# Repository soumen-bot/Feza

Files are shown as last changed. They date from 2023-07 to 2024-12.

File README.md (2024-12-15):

# Feza

Constructed a UAV with S1223 airfoil that adhered to the requirements of SAE, India. The UAV was launched manually
from a circular location, which necessitated a focus on controllability during the design process. Priority was given to weight
optimization for the payload and ensured structural strength, while simultaneously striving for innovation

Final_draft.pdf has the final desing report for our UAV. 

Will be uploading video of flight and xflr analysis files soon

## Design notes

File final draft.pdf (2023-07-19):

DRONE DEVELOPMENT CHALLENGE 2023

DESIGN REPORT

DDC20230185 –
FEZA TEAM
MEMBERS

### 1. Marpati Varun Reddy 2. Mogli Pranav 3. Soumen Sinha 4. Vaishnavi Neela 5. Prem Ningombam 6. Vaibhav Naidu 7. Kshitij Gawande 8. Sravani Prabhala 9. Mallinath Ogirala

Survey No: 62/1A, Bahadurpally, Jeedimetla, Hyderabad, Telangana 500043

Dr Prasad Pokkunuri
Faculty Advisor

DATE (18 March 2023)

STATEMENT OF COMPLIANCE _

### SAEISS DRONE DEVELOPMENT CHALLENGE 2023

Certification of Qualification
Team Name | FEZA
Team ID | DDC20230185
College/University | Mahindra University
Faculty Advisor | Dr Prasad Pokkunuri
Faculty Advisor’s Email | prasad.pokkunuri@mahindrauniversity.edu.in

Statement of Compliance

As Faculty Advisor:

I certify that the registered team members are enrolled in collegiate courses.

I certify that this team has designed, constructed and/or modified the radio-controlled airplane with the intention to use this aircraft in the SAEISS Drone Development Challenge 2023 competition, without direct assistance from professional engineers, R/C model experts or pilots, or related professionals.
I certify that this year’s Design Report has original content written by members of this year’s team.
I certify that all reused contents have been properly referenced and is in compliance with the University’s plagiarism and reuse policies.
Signature of Faculty Advisor | Date (18 March 2023)
Signature of Team Captain | Date(18 March 2023)

Team Captain Information
Team Captain Name | Marpati Varun Reddy
Team Captain’s Email | Varunreddy00412@gmail.com
Team Captain’s Mobile: | 9110510760

Table of Contents

1. Appendix | 0
2. Introduction | 5
3. Objective | 5
4. Mission Parameters | 5
5. Research | 5
6. Airfoil Selection | 6
a. analysis | 6
b. wing airfoil | 6
7.wing planform | 7
8.wing configuration | 8
9.Wing loading and area selection | 8
10. Tail | 10

### 11. stability

a. final stability configuration | 12
12. electronics | 14
a. motor and esc selestion | 14
b. servo sizing | 18
c. battery selection | 18
d. red armin plug | 19
13. design | 20

a fuselage

19

20

b tail | 21
14 control surface sizing | 22
a ailerons | 22
b elevator | 23
c rudder | 24
15 manufacturing | 24
a material selection | 24
b packing box | 27
16 weight built up and balance | 29

APPENDIX

- v = Velocity of the aircraft.
- g = Acceleration due to gravity.
- Ws = Wing loading in kg/m2
- ρ = Density.
- b = Wing span.
- c = Mean aerodynamic chord length.
- S = Wing area.
- α = Angle of attack.
- Cm = Coefficient of moment.
- CL = Coefficient of lift.
- CMα = Coefficient of moment per degree of angle of attack.
- CLα = Coefficient of lift per degree of angle of attack.
- VH = Tail volume ratio (Horizontal).
- Vvt = Tail volume ratio (Vertical).
- Xn.p. = Distance for neutral point.
- Xc.g. = Distance for center of gravity.
- η = Efficiency of the tail.
- ε = Downwash angle.
- Iw = Wing setting angle.
- It = Tail setting angle.

### 1. INTRODUCTION

The report details the unmanned aerial vehicle (UAV) created by Team Feza for the 2023 Drone Design

Challenge organized by the Southern Section of the Society of Automotive Engineers India (SAEISS). The

competition's objective is to provide engineering students with practical challenges that they may encounter

during their academic tenure by tasking them with researching, developing, designing, constructing, and

producing a prototype of a fixed-wing UAV that meets the practical and mission requirements specified by

SAEISS. The process also enables students to acquire vital technical and interpersonal skills.

### 2. OBJECTIVE

Team Feza's objective was to construct a UAV that adhered to the requirements outlined in the rulebook.

The UAV would be launched manually from a circular location, which necessitated a focus on

controllability during the design process. The team also prioritized weight optimization for the payload

and ensured structural strength, while simultaneously striving for innovation.

### 3. MISSION REQUIREMENTS

SAEISS aimed to motivate undergraduate students to create a UAV capable of lifting the maximum

payload according to the specified regulations. The UAV's weight limit, not including the payload, was

set at 1.5 Kgs, and it had to fit inside a box with sides less than 3ft. The UAV had to be launched

manually from a designated launch circle and complete a full 360 circuit using only a 3s battery for

power.

### 4. RESEARCH

Our team has been participating in the micro class for three generations now and in the past, we prioritized

the assembly of parts and structure. For our last project, we opted for a high wing rectangular configuration

and utilized a complete monocoque fuselage. However, this time around, we aimed to simplify the design by

utilizing a side paneled fuselage and adhering to the SAEISS rule book and Micro class constraints. Our

inspiration came from the manufacturing processes of last year's Regular and Micro planes. Previously, we faced challenges in achieving a balanced center of gravity and installing the battery. To simplify the

assembly process, we have designated specific positions for electronics and created separate holding spaces

for them.

### 5. AIRFOIl SELECTION

a. analysis

To narrow down the list of previously chosen airfoils, a number of flight determining factors are taken into

account. These factors include the Coefficient of lift at ‘0’ angle of attack, Stall angle, Maximum coefficient

of lift, Manufacturing limitations, and the Average drag coefficient across a range of Reynolds numbers. The

analysis is conducted using Reynolds numbers ranging from 10,000 to 500,000 and an angle of attack

between -10 to 30 degrees.

b. Wing airfoil

To pack as much lifting capabilities in to the plane, Airfoils with high cl values at low Reynolds-number are

researched. For preliminary analysis of wing and horizontal stabilizer options, several cambered airfoils were

considered. These included EPPLER's E423, E421, and E420, SELIG's S1223, S1223rtl, and S2027,

WORTMANN's FX74-CL5-140 and FX63_137, AG35, CH10, NLF 0115, NACA 6409, Kenmar-il, Kc135

winglet, and LNV 109 A. After evaluation, EPPLER's E423, E421, and E420, SELIG's S1223 and S1223rtl,

and CH10 were found to have the highest capabilities for cl and cl/cd at low Reynolds numbers. Of these,

S1223 had the highest cl, as well as a high Cm. Despite the high Cm, the team chose to go with a high Cl

airfoil in order to build the plane as compactly as possible.

S1223 –

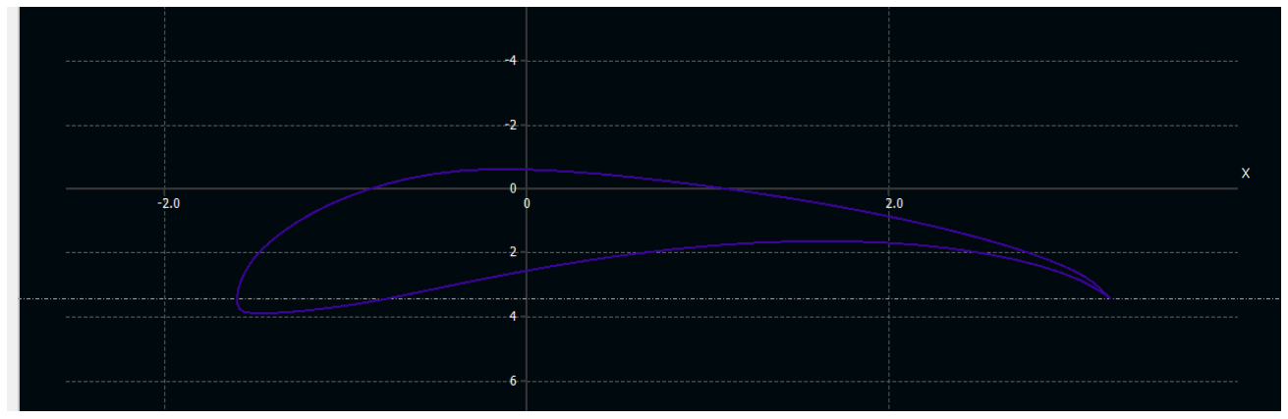
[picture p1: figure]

Thickness | Max. Thick.pos. | Max. Camber | Max. Camber pos.
12.14% | 19.82% | 8.67% | 49.05%

Table:1 tabular data of the shape of the Airfoil S1223

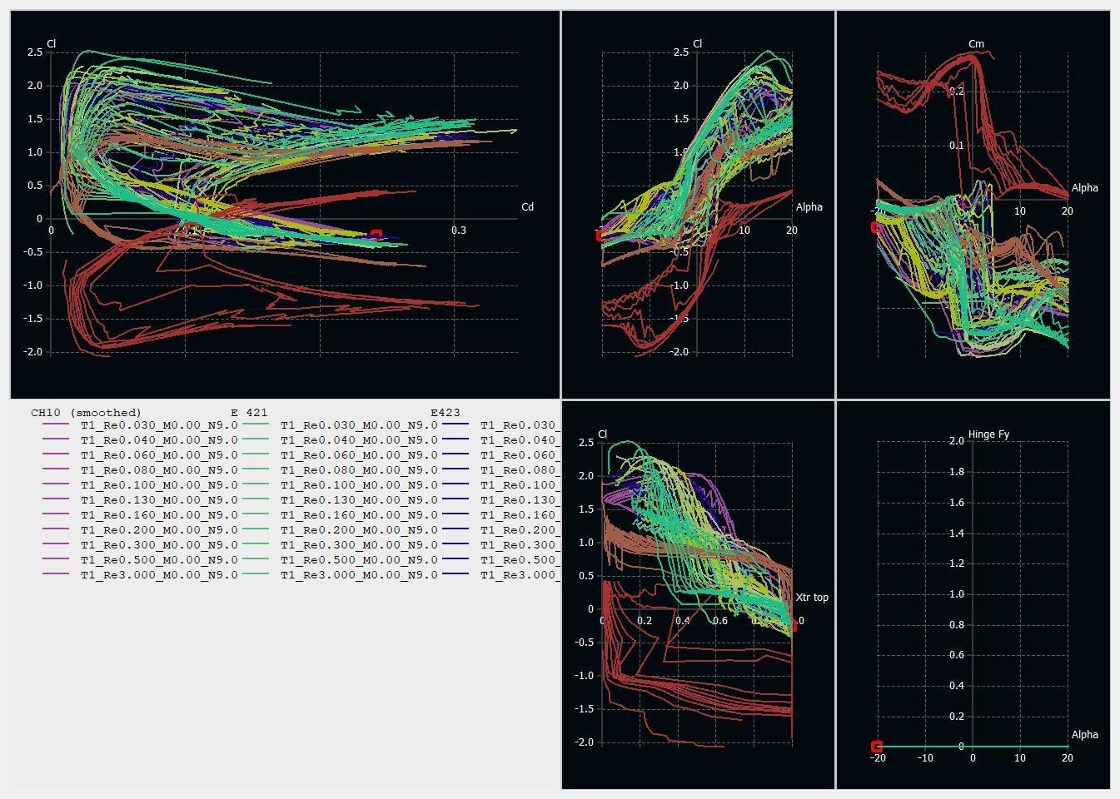
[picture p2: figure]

The graphs above primarily show the relationships between cl and cd, cl and alpha, and cm and alpha for types of foils: S1223 and NACA0012. EPPLER's E423, E421, E4203 and S1223rtl, and CH10

### 6. WING PLANFORM

After conducting a detailed analysis and comparing different planforms, a rectangular wing configuration was

selected. The comparison revealed that the drag reduction offered by a tapered wing over a rectangular wing was

minimal. Additionally, while elliptical wings have the advantage of stalling uniformly across the entire wing

instead of at the tips first, manufacturing them is more complex than a rectangular wing. A delta wing was not

chosen due to the stringent design, size, and manufacturing requirements it demands.

### 7. WING CONFIGURATION

The High wing configuration has been selected among the three options of Low, Mid, and High wing.

This is because of its inherent keel effect or pendulum effect, resulting from the center of gravity being

lower than that of the center of lift. Additionally, the Low wing configuration is avoided to prevent the

UAV from landing on its wings. Furthermore, manufacturing the Low and Mid wing configurations to

be longitudinally stable can be challenging. Based on our past experience with a Mid wing

configuration, the UAV began to wobble and flutter its wings, whereas the High wing configuration

offers a slight advantage for easy reinforcement. Another design advantage of the High wing

configuration is that the wing can be slid on top of the plane and secured to complete the aircraft.

### 8. WING LOADING AND AREA SELECTION

Wing loading is the ratio of Aircrafts weight to its area. It helps determining the stall speed of the aircraft

the above equation gives us the wing loading

Assume Cl =0.762 . ρ = 1.29 , ( values of Cl and ρ are chosen so that they cover most of

the range of the flight.)

Table 5.1: Velocity vs Wing loading of the aircraft
Velocity (m/s) 5 | 7.5 | 10 | 12.5 | 15 | 17.5 20 | 22.5

Wing

loading (kg/m²

)1.25 | 2.82 5.01 7.83 | 11.28 | 15.35 20.06 25.38

A step size of 0.25Kg is considered to calculate the wing area at different

velocities that can be acquired from hand launch, with plane weight up to 3 Kgs

Table 5.2: Area of the wing in m² based on weight and velocity of the aircraft.

Velocity (m/s) | 5 | 7.5 | 10 | 12.5 | 15 | 17.5 | 20 | 22.5
Mass = 1.5 kgs 1.2 | 0.53 | 0.29 | 0.19 | 0.132 0.09 | 0.074 0.059
Mass =2 kgs | 1.6 | 0.70 | 0.39 | 0.255 | 0.177 0.13 | 0.099 0.078
Mass = 2.5 kgs 2 | 0.88 | 0.49 | 0.319 | 0.221 0.16 | 0.124 0.098
Mass = 3 kgs | 2.4 | 1.06 | 0.59 | 0.383 | 0.265 0.195 0.149 0.118

We fixed our wingspan to be 120 cm to accommodate the wing loading capacity and still

be able to fit in the box with all sides less than 3ft, through extensive analysis by XFLR5

we arrived at a wing span of 0.25m²
that is a chord length of 25 cm.

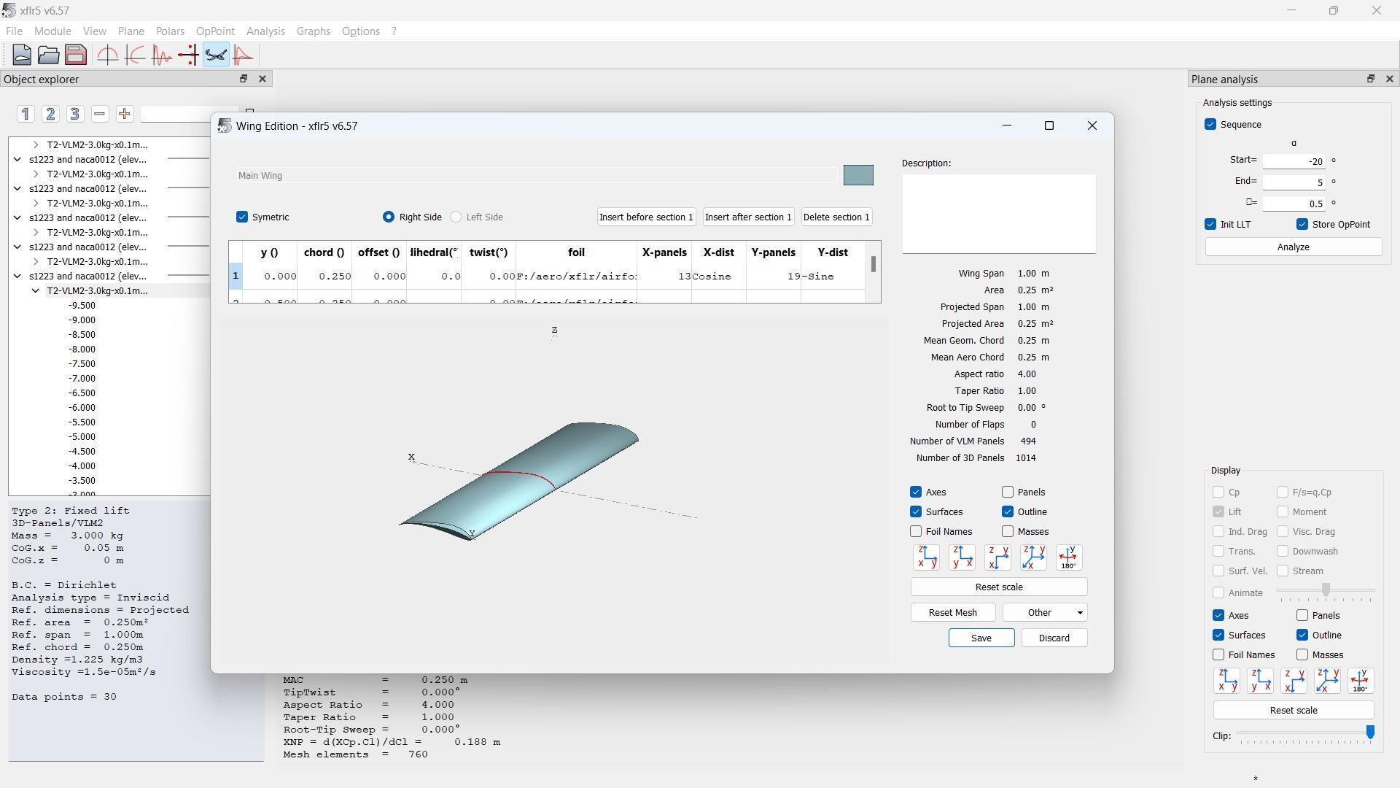
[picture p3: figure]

### 10. Tail

We chose to use the standard Tail configuration for our plane, which consists of two components -

the horizontal stabilizer and the vertical stabilizer. These parts play a critical role in guiding and

maneuvering the plane during flight. The Tail is an essential part of the plane that helps to maintain

its orientation and keep it on the desired flight path in a passive manner. This is achieved by

generating a moment around the Cg (center of gravity) through the deflection in orientation caused

by any disturbances.

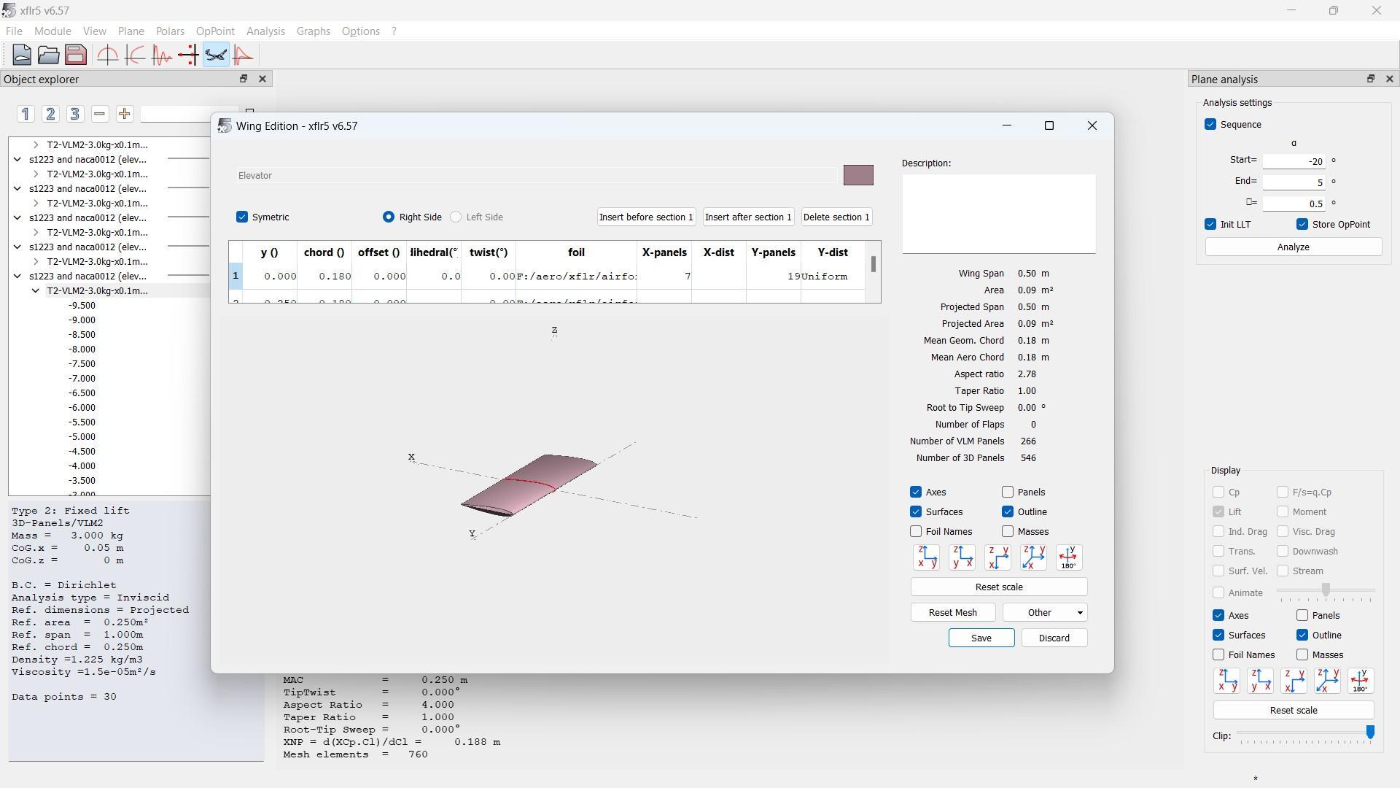
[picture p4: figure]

We decided to use the NACA0012 airfoil for the elevator of

our plane due to its effective production of pitching moment and minimal drag. Our objective was

to minimize the size of the horizontal stabilizer while still balancing the wing moment, and as a

result, we were able to achieve satisfactory longitudinal stability.

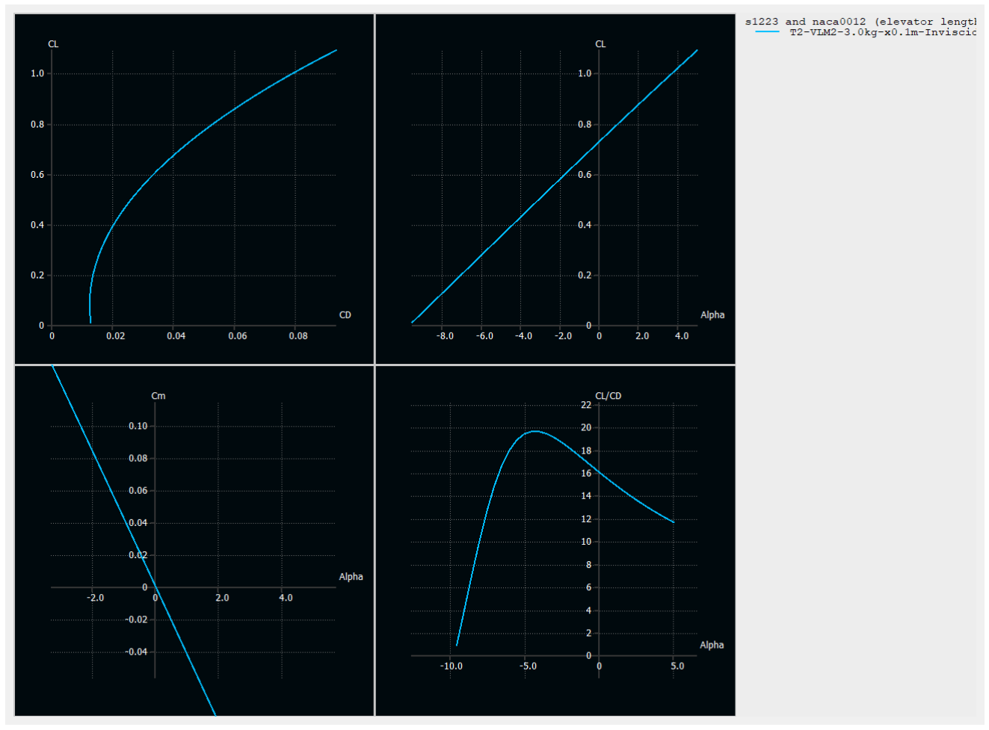
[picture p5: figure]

the above picture gives you the flight characteristics of our plane

FINAL STABILITY CONFIGURATION

After the detailed and calculate evaluations of all the possible configurations of tail and the area of

wing being 0.25 m2,the following configuration of the plane was achieved:

Table: Aircraft properties for stability configuration.

Name | Class | Numerical Value

Wing Properties

Chord Length

Wing area

Wing span

Wing setting angle

0.25m

0.25 m2

1.2m

0

Horizontal tail properties | Chord Length Tail span Tail setting angle | 0.180m 0.5m 0
Vertical tail Properties | Chord Length Tail Span | 0.180m 0.25m

### 1. Electronics

a. Motor and ESC selection:

After considering the mission objectives and regulations, we opted for a DC brushless outrunner motor

with a low kV rating. We selected a low Kv motor because it is more suitable for airplanes that fly at

slower speeds, as it provides higher output torque. This enables us to use a larger propeller with a small

pitch, which is typically used in short takeoff and landing aircraft. In our decision-making process, we

also took into account the weight of the aircraft, including any cargo, the necessary thrust (keeping battery

limitations in mind), and the required power output.

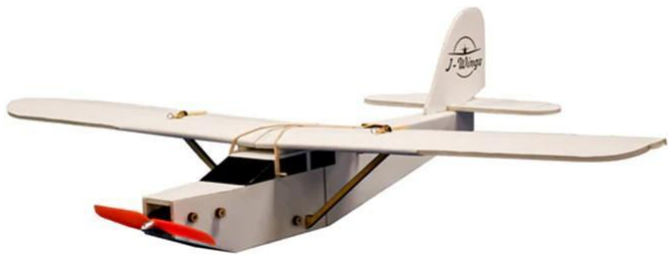
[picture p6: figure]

Type of airplane | Thrust-to-weight ratio
Glider/Trainer | 0.35 to 0.55
Scale Flight | 0.60 to 0.70
Sport and Slow acrobatic | 0.70 to 0.80
Acrobatic | 0.80 to 1.00
Jets and 3D | 1.00 to 2.5

Our study found that the correlation between power (measured in watts, W) and thrust (measured in grams,

g) is directly linked to the Kv rating of the motor. Nonetheless, the scatter of data points in the graph may

differ depending on the propeller pitch. Fundamentally, when the Kv rating increases, a greater amount of

power is needed to produce the same thrust. This is because using a higher Kv motor necessitates a

reduction in propeller diameter.

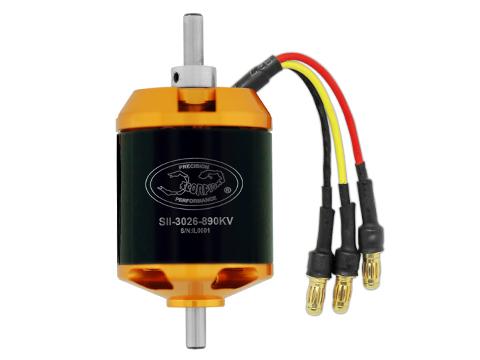
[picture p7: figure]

Once you know the weight of your aircraft, the process consists of several steps:

- Determine the desired thrust-to-weight ratio.
- Calculate the amount of thrust required for your plane.
- Decide on the desired speed of your aircraft (fast or slow).
- Choose a Kv value that aligns with your objectives.
- Use the Kv value to identify the Power/thrust ratio.
- Determine the power (in watts) required to generate the necessary thrust.
- Based on the selected values for Kv, thrust, and power, select a motor from a

reputable manufacturer.

·Either follow the recommended propeller specifications for the chosen motor or use an

appropriate method to select a suitable propeller.

Calculating thrust:

Thrust= Weight*thrust/weight ratio | (The thrust/weight ratio of an acrobatic plane

is 1)

Thrust= 1900*1 = 1900g of thrust

As mentioned in the beginning of this section, we prefer a low kv value motor because it better suits

the plane that fly at slower speeds. So, we chose a motor the 1000kv specification.

To go further in selecting a motor, we need the power of our motor.

Calculating power:

Power = thrust* power/thrust ratio

Power/thrust ratio=

0.17*(kv/1000)+0.09

=0.17*(1000/1000)+0.09

=0.26w/g

Now, going back to calculating power:

Thrust is found to be 1900g. => 1900*0.26= 494 watts

So, in conclusion, referring to the calculations made, we are looking for a motor with the following

specifications:

1. 1000kv
2. 1900g of thrust
3. Wattage of 494w.

The motor we finalized isScorpion SII-3026-890KV (V2)

[SII-3026-890KV]

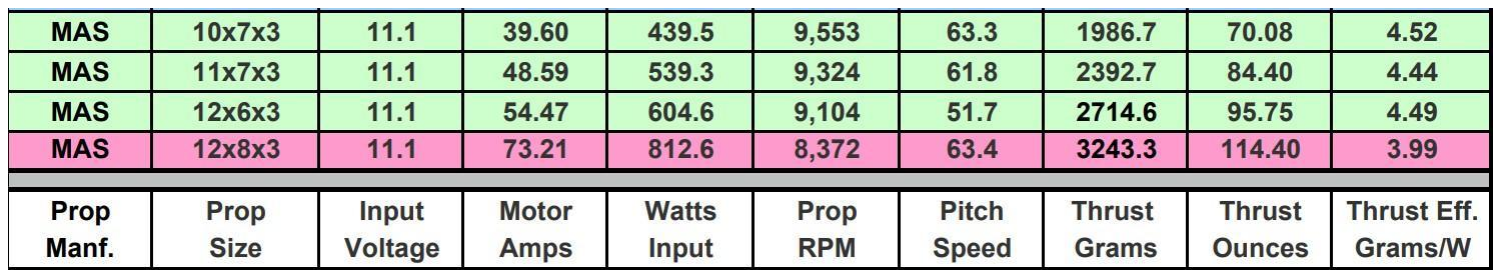
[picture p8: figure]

The essential factor to consider while choosing an ESC was that the motor would not

draw more current than the ESC's maximum rating. The motor consumes 70A of current

at maximum power. We picked a Readytosky 80A ESC 2-6S Brushless ESC Speed

Controller

which can support 80A rating based on this

b. Servo sizing:

The selection of servos for our aircraft is dependent on various factors such as the weight of the

flight, the dimensions of the wing, and the required thrust. Additionally, we take into consideration

the sizing of control surfaces and the type of battery used. The decision to choose a specific servo is

also influenced by its rated speed, supply voltage, and the amount of output torque required.

C

2V

2L sin(s1) tan(s1)
T = 8.5 × 10
−6 ( | tan(s2)

)

c. Battery selection
The battery was selected based on the restrictions according to the rulebook supplied and the

requirements of the motor and servos selected such that it be sufficient for a 5-minute flight

keeping a 20% error margin. With maximum current required as 36A, 3S (due to rule book

restrictions) 11.1V and the motor selected we researched batteries and decided to use the Orange

2200mAh 3S 30C/60C Lithium polymer battery Pack (LiPo) as it best fit our requirements and

the manufacturer was well known for its quality.

d. Red arming plug
An arming plug, essential for safety, is a small plug, fit in the flight hardware to enable functions

that, for instrument or personnel safety. Arming switches are used for isolating the battery from

outside of the aircraft. The arming plugs are fabricated by the team to facilitate enough wiring

length and to accommodate xt60 male plug from battery and bullet connectors from ESC and The

necessary holes have been made for installation during flight so that it can be easily activated

before flight.

### 13. Design

During our previous participation in the competition, we utilized a monocoque structure to

construct a lightweight aircraft. However, we faced challenges in installing the necessary

electronics such as the battery and ESCs. To overcome these difficulties, we opted to build a

sidepaneled fuselage that resembles a rectangular

box-like structure for this year's competition. Our previous fuselage design consisted of two major

elements, which were the ribs and longerons, and we avoided using stingers to reduce the

complexity of the chassis. For this year's competition, we simplified the manufacturing process by

eliminating all the ribs and spars, and instead, we constructed a high wing configuration plane.

a. Fuselage

Our goal for the fuselage was to achieve both durability and lightness. After careful deliberation, we

determined that implementing a truss system would be the most effective solution. This approach

would enable us to reduce the amount of material required while still maintaining the necessary

structural integrity. Our team conducted extensive research to acquire a comprehensive

understanding of truss systems and to develop a suitable design for the fuselage. One of the

innovative ideas we implemented this year was applying the truss theory to reinforce the

structural strength of the fuselage.

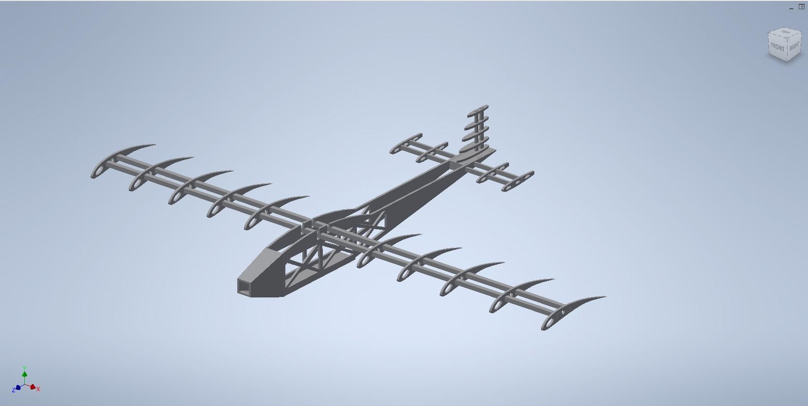
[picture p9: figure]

b.Tail

This year, we created a high-quality CAD design for the tail of our aircraft, which utilizes an innovative

approach where the fuselage walls are connected by a V-shaped ramp structure that can support both the

horizontal and vertical stabilizers through intrusions. With this design, we expect to have decreased the

amount of stress and shear on the tail compared to previous designs, and also made it easier to attach the

rudder and elevator with less effort and time required during the plane manufacturing process.

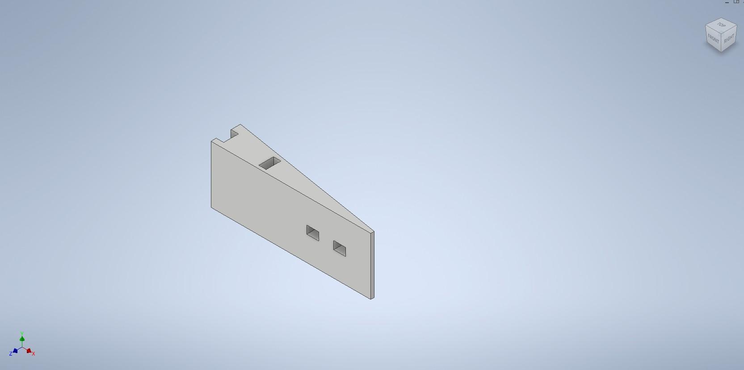
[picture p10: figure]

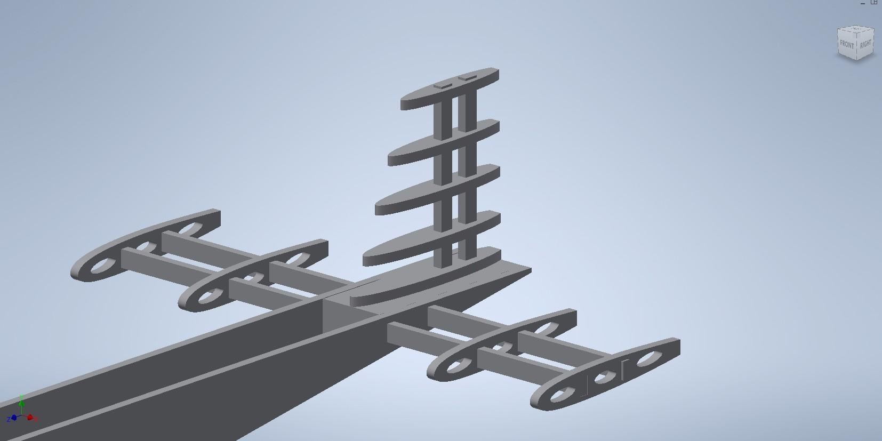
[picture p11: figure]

### 14. CONTROL SURFACE SIZING

AILERONS:

The 4 main parameters to be considered while designing the ailerons are the aileron planform

area (Sa), the aileron chord/aileron span ( Ca/ba), the maximum up and down deflection ( +(or)-

Dmax ), and the location of inner edge of aileron along the wing span (bai).

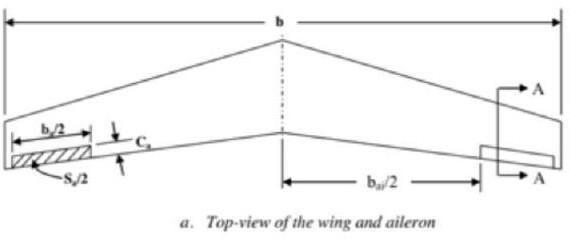
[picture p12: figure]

To set the proper dimensions of the ailerons a general guideline was followed. The typical

values for these parameters are as follows:

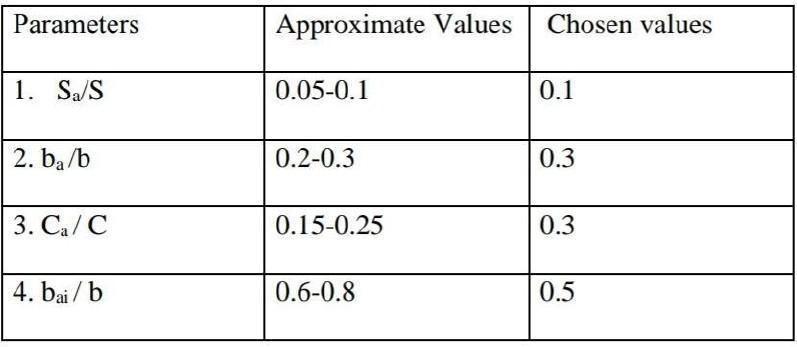
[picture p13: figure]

The value of Sa/S (area of ailerons by area of wing) was taken as 0.1. This was to maximise area of the aileron to minimise time to achieve a certain bank angle, resulting in a higher manoeuvrability.
The
issue with having a larger aileron is the load the actuators have to take will be higher. Thus, servo sizing was crucial.
The ratio of ba/b (aileron length to wing span) was taken as 0.3 based on other aircraft data. The ratio of Ca /C (aileron chord length by wing chord length) was taken as 0.3. The area of the aileron was to
be around 0.1 of the wing area. Thus, ba and Ca were varied to ensure an optimal case for a
desired area. The ratio of bai/b was taken as 0.5 to ensure the aileron doesn’t end at the wing tip.
This was to decrease excess wing tip vortex, which is caused due to the aileron ending at the wingtip. The aerodynamically accepted range of maximum deflection of the ailerons is 300. Increasing the angle beyond this would cause flow to separate, causing the surface to stall.
Thus, after running multiple iterations, it was decided the aileron would have the following values Ca = 75 mm ba = 600 mm bai = 180 mm
Thus, ailerons dimensions were 180 mm x 75 mm. Positioned at distance of 120 mm from either wing tip.
a. Elevator:
The rule of thumb is that the elevator should be 10%-25% of the area of the horizontal stabilizer. We chose the lower bound to keep the area of the elevator as less as possible so as to ensure less sensitivity to flying environments. Essentially, the span of the elevator=span of horizontal stabilizer. Only the chord of the elevator will be different. Length of chord=20% of length of chord of horizontal stabilizer. As the horizontal stabilizer was designed to have a span of 300 mm and a chord of 75 mm, the elevator was sized at the

following□ span = 0.5m

chord = 0.180m

a. Rudder:
The rule of thumb is that the rudder should be 10%-25% of the area of the vertical stabilizer. We chose the lower bound to keep the area of the rudder as less as possible so as to ensure less sensitivity to flying environments. So, the span of the rudder=span of vertical stabilizer. Only the chord of the rudder will be different. Length of chord=20% of length of chord of vertical stabilizer. As the vertical stabilizer was designed to have a span of 150 mm and a chord of 75 mm, the rudder
was sized at the following
Span = 0.25m
Chord= 0.180m

### 16. Manufacturing

a. Material selection

As stated in the beginning of the report, the weight of the plane designed for ADC 2022 was barely within the stipulated limits. So, the team did an analysis of areas to reduce weight. Hence, research was done from scratch on the design which resulted in the selection of Balsa wood. Balsa wood is an orthotropic material often used for hobby level UAVs due to its light-weight and decent strength. The mechanical properties of Balsa are as follows:

Table 6: Mechanical Properties of Balsa Wood

Density | 0.16 g/cm³
Ultimate Tensile Strength | 1.00 MPa (perpendicular to grains) 73.00 MPa (Axial)
Compressive Strength | 1.00 MPa (Perpendicular to grain) 6.90-9.00 MPa (axial)

Flexural Modulus | 2.55-3.17 GPa (Static Bending)

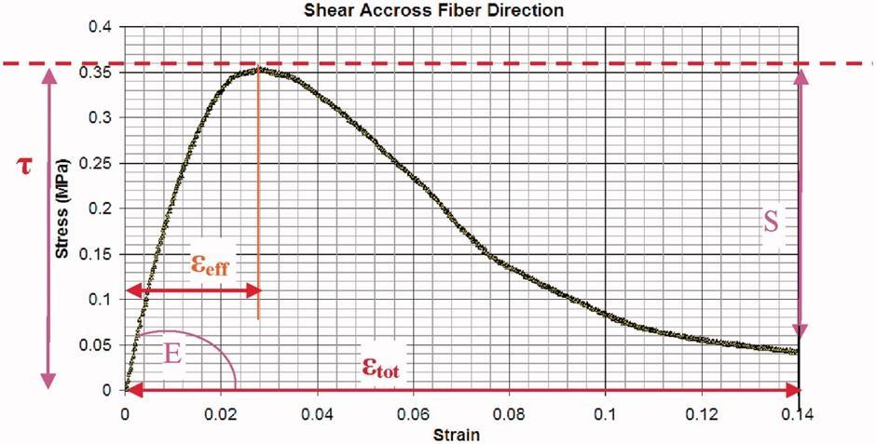
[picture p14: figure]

Fig: Characterization of balsa wood mechanical properties required for continuum damage mechanics analysis

In order to ensure that the air foils of the wings, elevator, and rudder remain firmly attached to the spar, it is

imperative that the foundation is sufficiently strong. In our previous design, we utilized aero-ply as

longerons and found that they were durable enough to withstand crashes. After conducting several prototype

tests, we concluded that Aero-Ply would also make an excellent material for the spar that holds the airfoils

together in wing manufacturing.

Aeroply is made up of multiple layers of plies of birch veneer. The number of layers or plies depends on the thickness of the Birch plywood panel. The two outermost layers of Birch plywood are the face and back veneers, while the inner plies are the core stock.

Foam may be utilized in our model solely for the purpose of decreasing its weight. During the prototype production process, foam could be incorporated to minimize the weight of the model. The fundamental mechanical characteristics of foam materials include plateau stress (σP), elastic modulus (E), yield point, and densification strain, with material parameters represented by coefficients C and m. The mechanical properties of foam can be summarized as follows: "

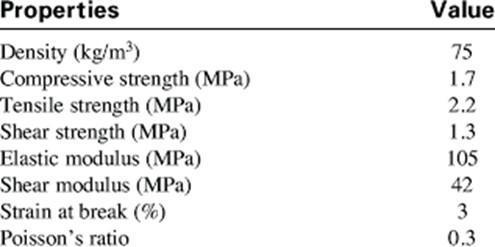
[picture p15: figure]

b. Packing box

We determined that a 3x3x1 ft container would be the ideal size for packing the airplane according to the

regulations. By placing the wing diagonally in the box, we can secure it properly. We can also secure the

fuselage and tail in one of the triangular halves, leaving the other half empty for securing other items such

as electronics, peripherals, and even spar parts and toolkits.

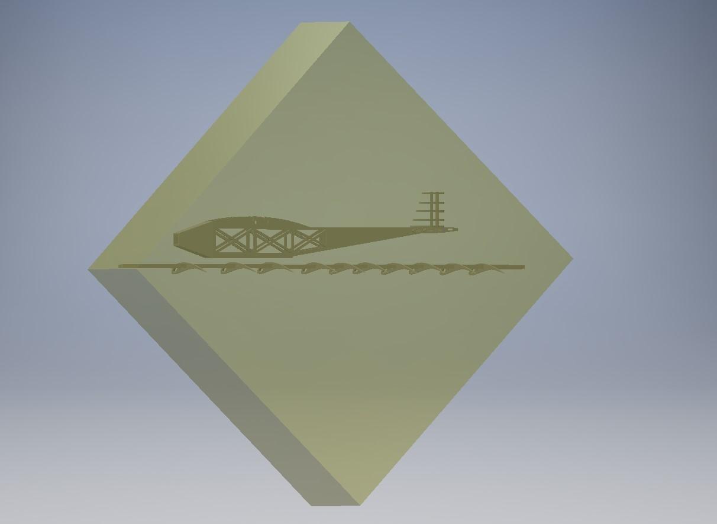
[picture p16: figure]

Figure 8 visual depiction of plane storage in box from

isometric view

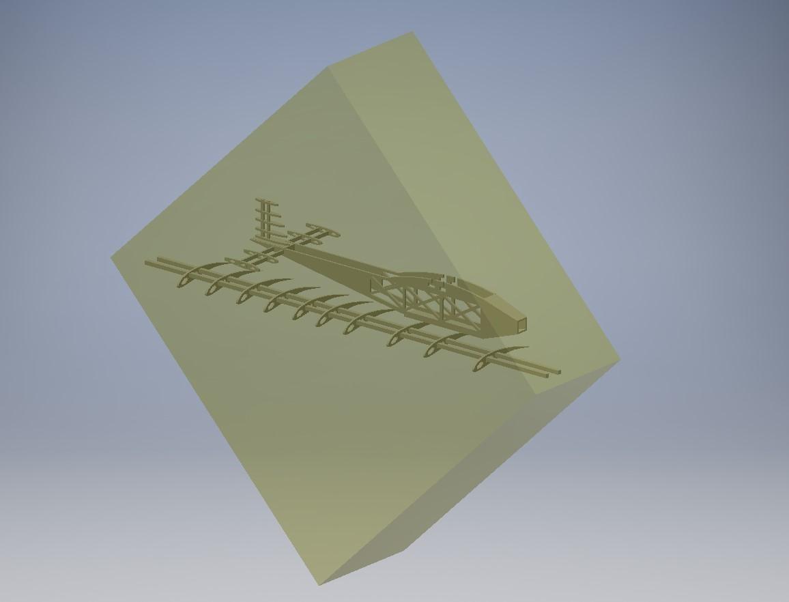
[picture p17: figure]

Figure 9 visual depiction of plane storage in the box

from top view

### 1. Weight Built up and balance

PART | QUANTITY | MASS (Kg)
MOTOR | 1 | 0.15
ESC | 1 | 0.08
SERVOS | 4 | 0.015
FUSELAGE + TAIL | 1 | 0.55
WINGS | 1 | 0.25
BATTERY | 1 | 0.2
TOTAL | | 1.245

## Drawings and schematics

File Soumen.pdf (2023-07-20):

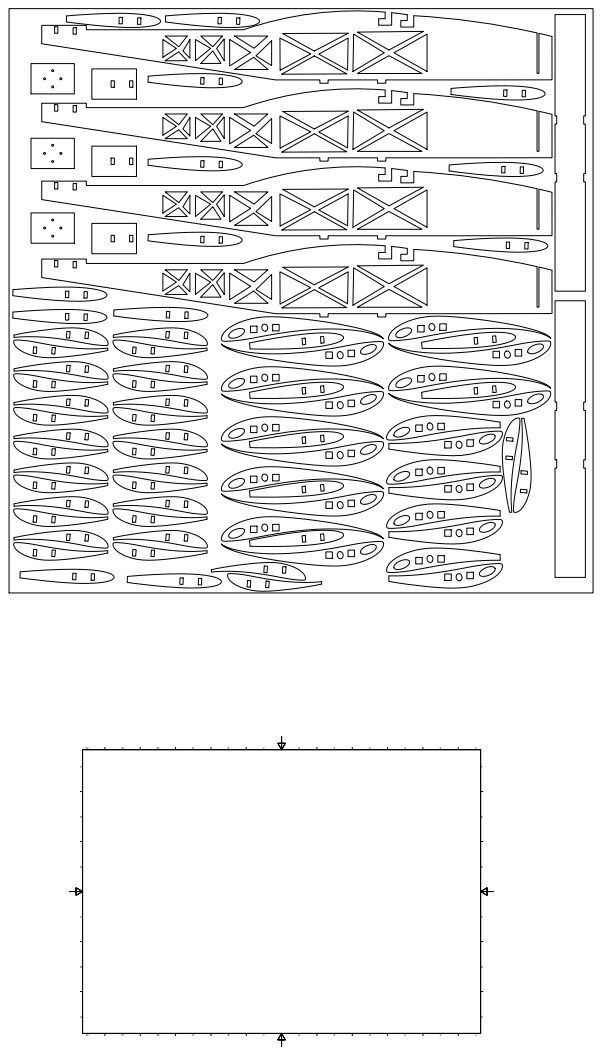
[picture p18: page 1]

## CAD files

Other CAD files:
Soumen.dwg
fusalage new.dwg
New base.ipt
back side foil.ipt
ddc final areoplane.iam
final side pannel.ipt
fusalage new.ipt
horizontal air foil.ipt
motor mount.ipt
new air foil.ipt
new air foil_MIR.ipt
tail plate.ipt
tail vertical rod.ipt
wing rod.ipt
